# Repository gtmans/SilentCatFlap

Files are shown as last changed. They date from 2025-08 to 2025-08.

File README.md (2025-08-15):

# SilentCatFlap (Sure Flap MOD)
My cat used to get startled by the loud click the flap made whenever his microchip was detected.
To solve this, I replaced the original motor with a 28BYJ-48 stepper motor that moves smoothly and quietly.

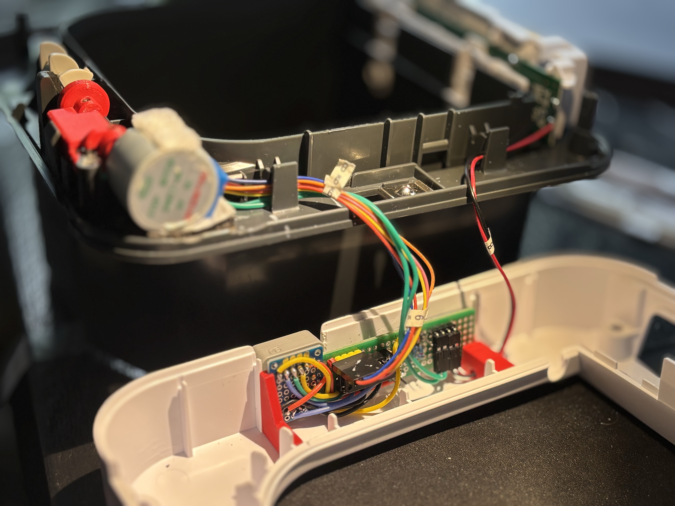
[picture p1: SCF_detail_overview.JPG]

The stock motor would drive loudly against a stop at -3 V to open and +3 V to close. In the first phase of the project, I kept as much of the existing cat flap electronics as possible, building a standalone controller that listens for those +3 V and -3 V signals and uses them to drive the stepper motor. The controller is powered by an M5 Atom Lite (about $10), which requires an external USB‑C power adapter. The stepper motor itself needs minor modifications — swapping the connector and removing a few protruding tabs.<BR><BR>

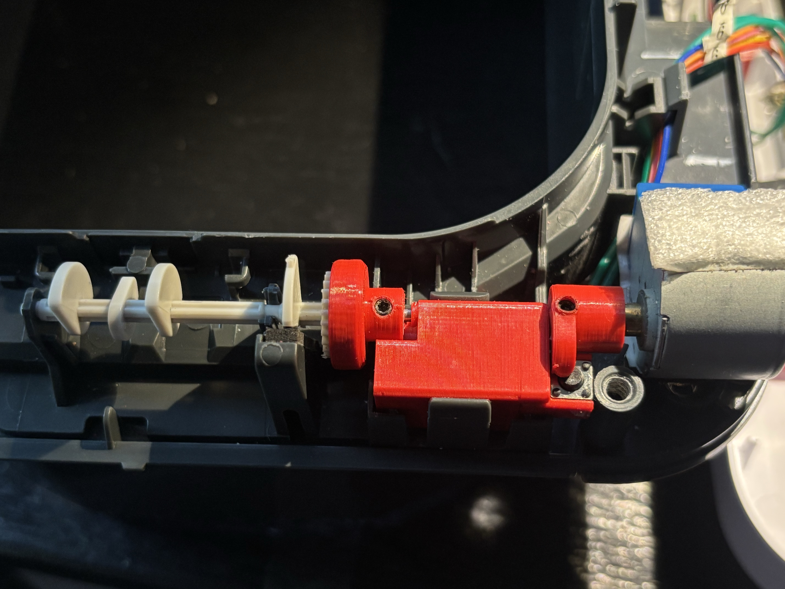
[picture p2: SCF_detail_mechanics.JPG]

From the accompanying ULN2003 driver board, I only use the driver IC, which I mounted onto a small custom PCB (see Fritzing layout). I also designed several custom parts for 3D printing (see .stl files). The build additionally uses a 2 mm shaft and two screws from a shaft collar, 3 10K resistors, 1 diode, some wire and a tiny microswitch.

Finally, a few small adjustments to the original cat flap housing are necessary to ensure that all moving parts operate freely.<BR>

tiny video: https://youtu.be/TwItX0s3qm8 <BR>Tinkercad model: https://www.tinkercad.com/things/aXRrV4Vo9WM-silentcatflap-parts-shared <BR><BR>
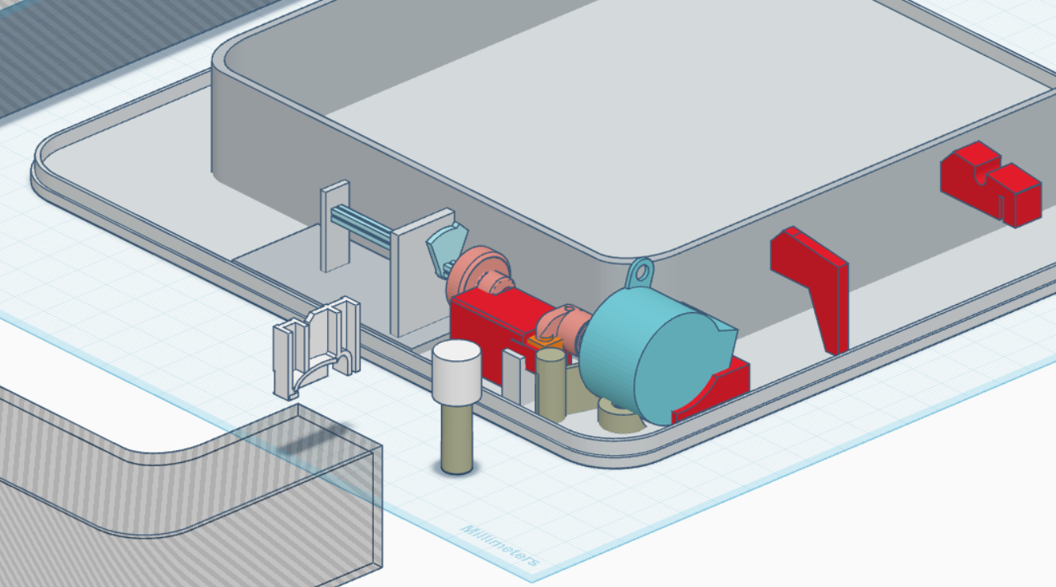
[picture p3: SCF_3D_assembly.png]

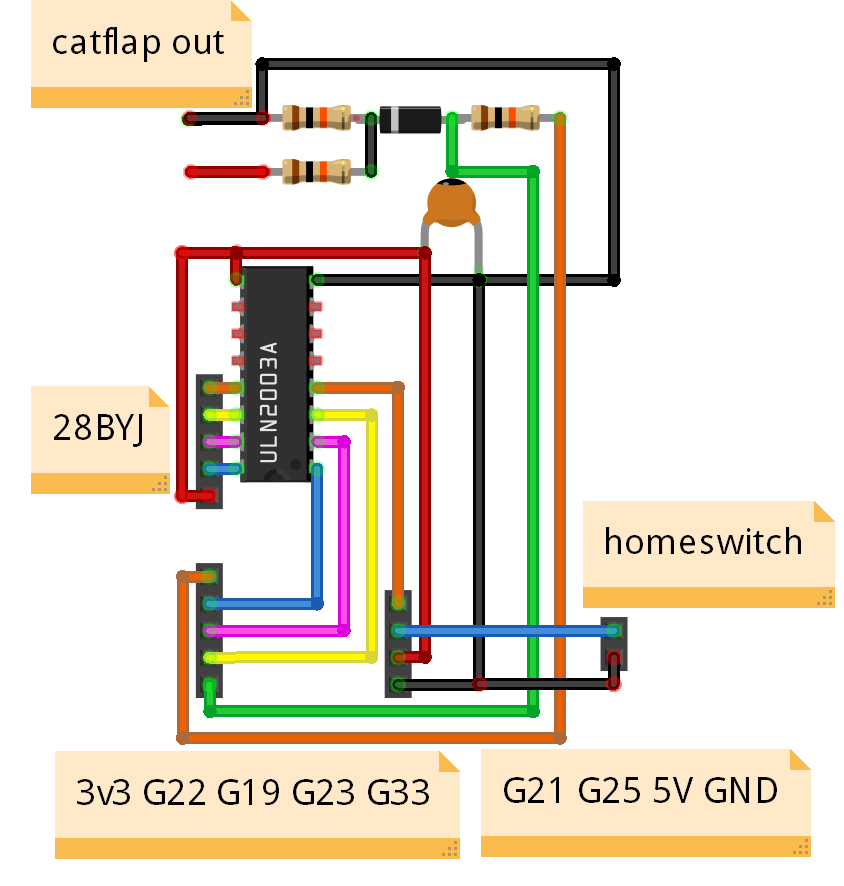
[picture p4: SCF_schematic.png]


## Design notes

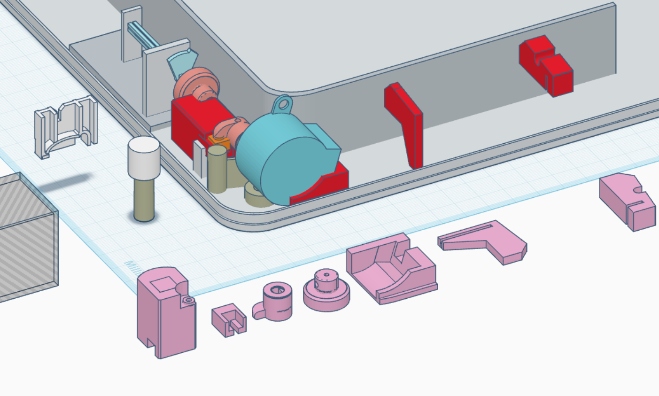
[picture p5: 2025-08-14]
SCF_3D_paerts_overview.png

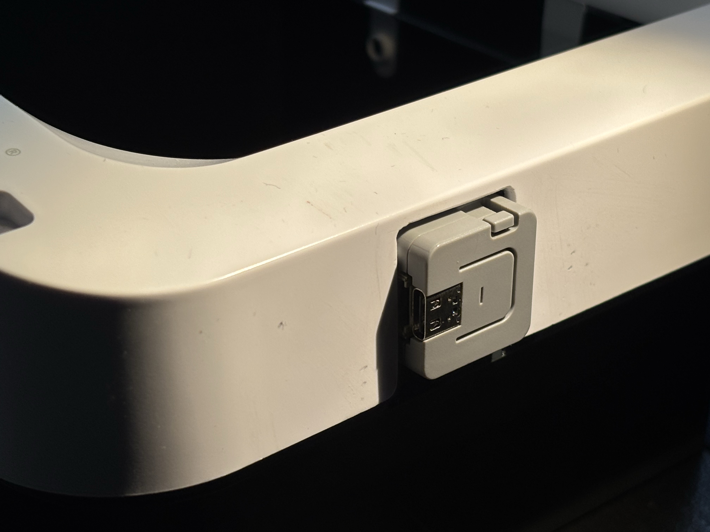
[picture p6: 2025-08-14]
SCF_detail_outside.JPG

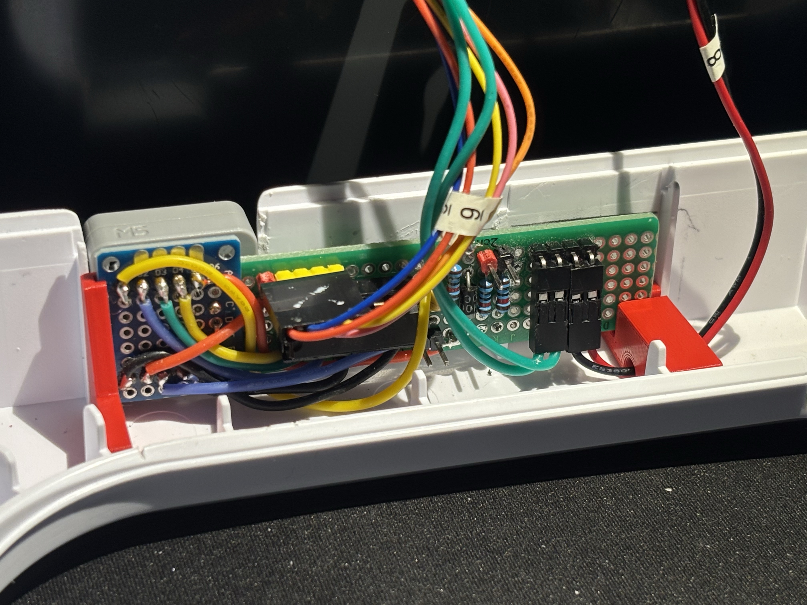
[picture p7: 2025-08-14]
SCF_detail_perfboard.JPG

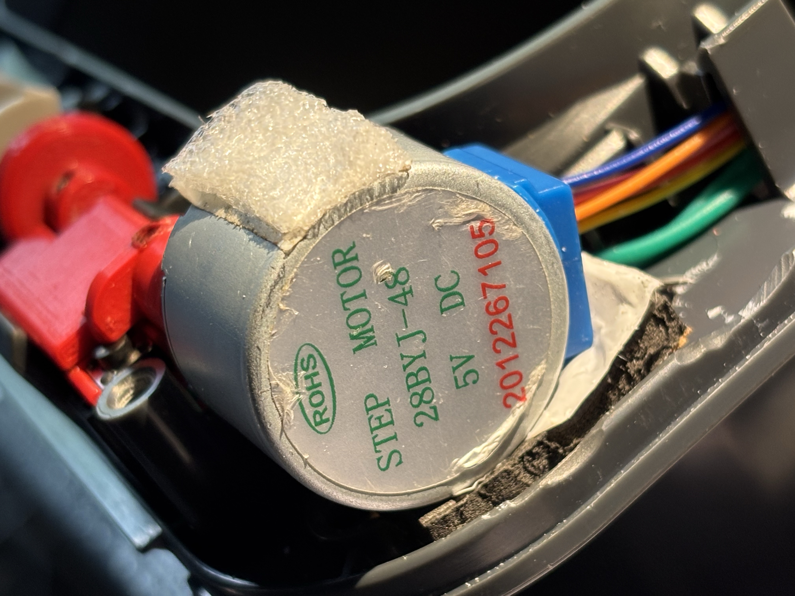
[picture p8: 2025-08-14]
SCF_detail_steppen.JPG

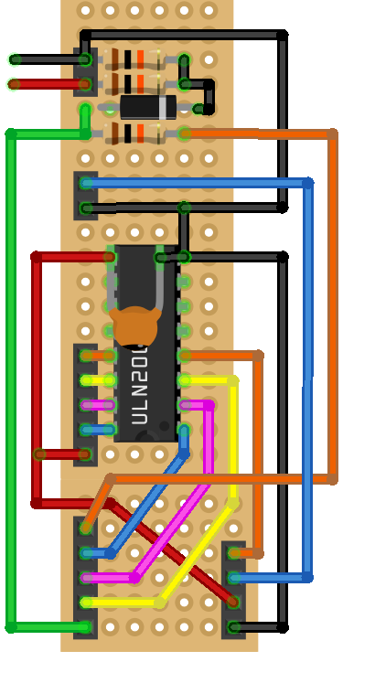
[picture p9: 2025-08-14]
SCF_perfboard.png

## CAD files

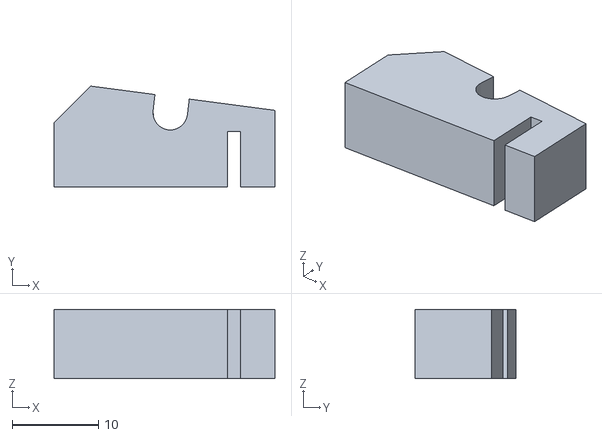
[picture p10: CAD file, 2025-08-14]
SilentCatFlap-print_holder1.stl
25.6 x 11.7 x 8.00

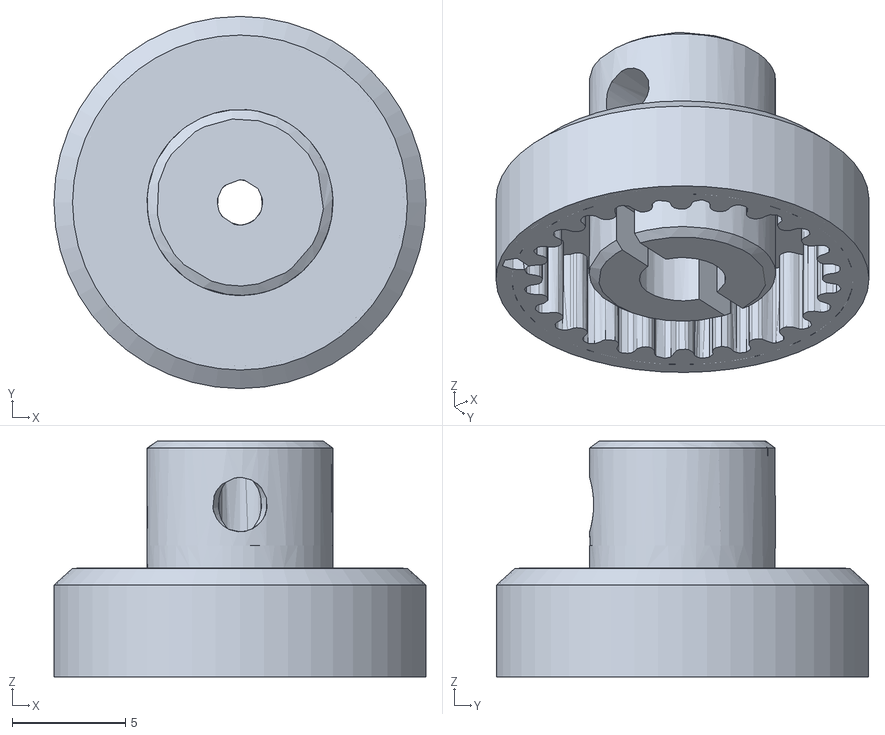
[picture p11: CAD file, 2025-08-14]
SilentCatFlap-gear_wheel.stl
16.4 x 16.4 x 10.4

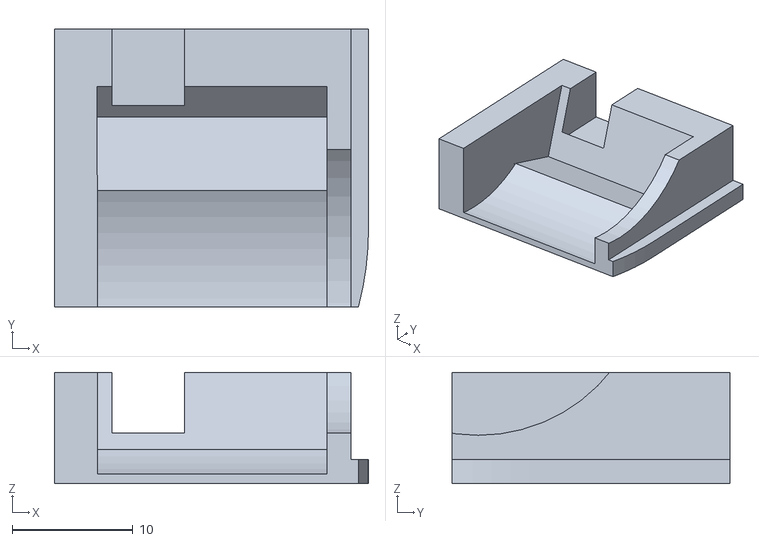
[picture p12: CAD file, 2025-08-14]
SilentCatFlap-steppen_holder(not used).stl
26.0 x 23.0 x 9.20

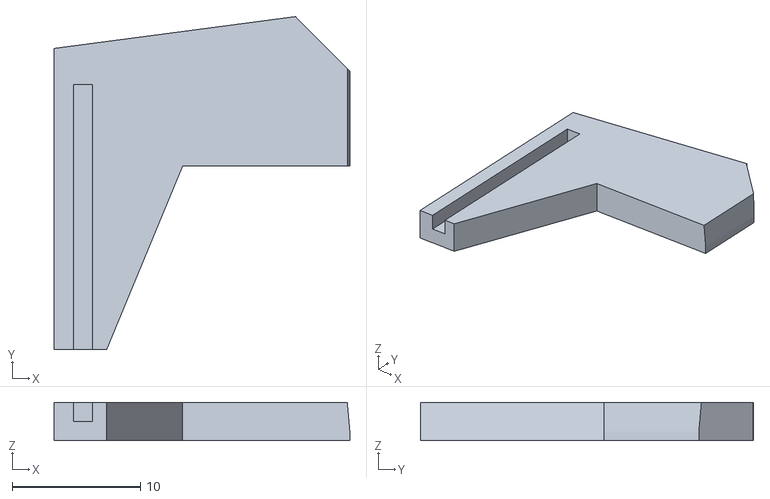
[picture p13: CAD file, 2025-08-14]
SilentCatFlap-print_holder2.stl
23.1 x 26.0 x 3.00

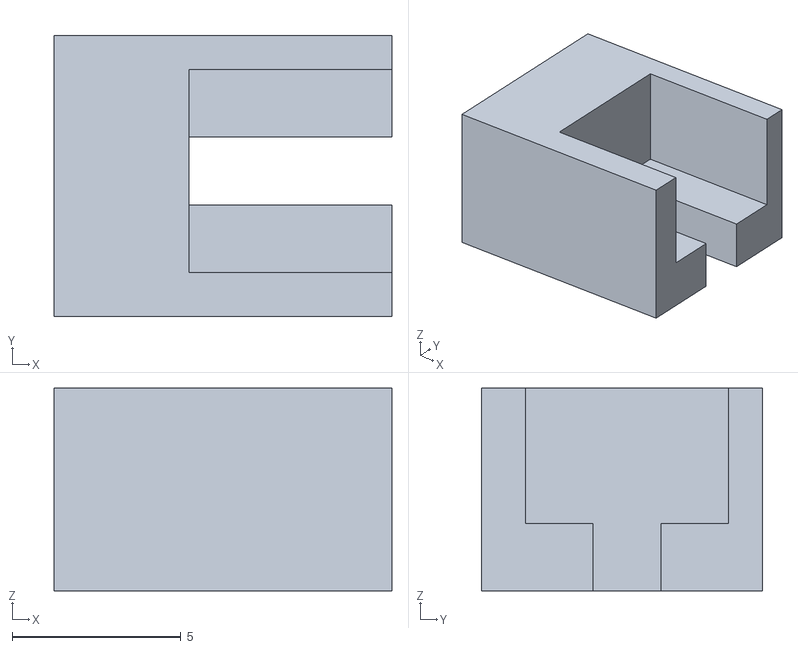
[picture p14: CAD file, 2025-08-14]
SilentCatFlap-switch_holder.stl
10.0 x 8.30 x 6.00

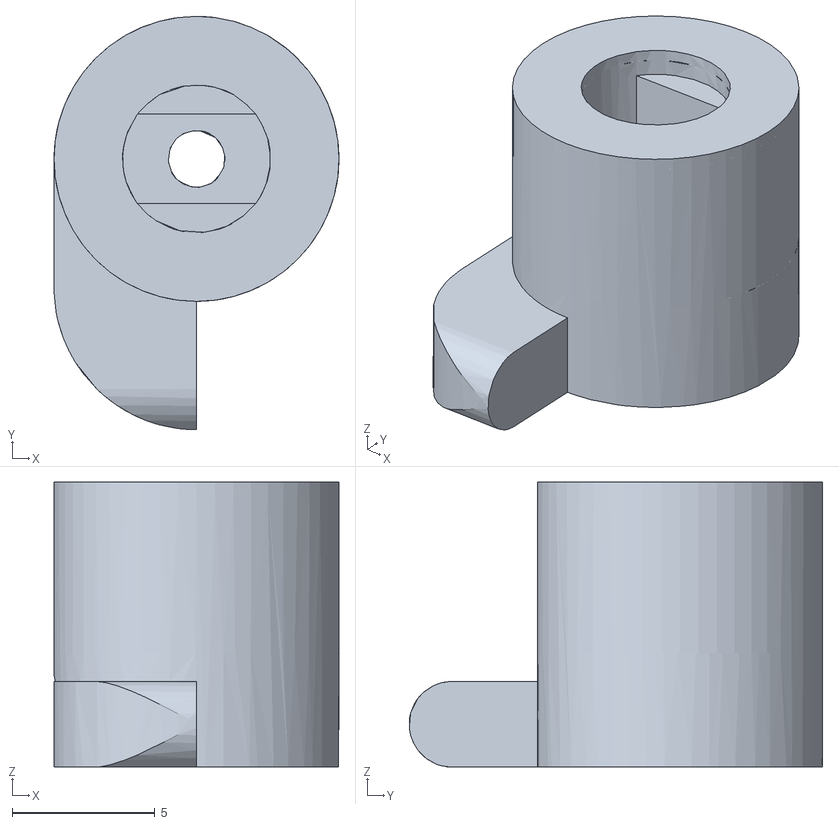
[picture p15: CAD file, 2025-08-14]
SilentCatFlap-steppen_wheel.stl
10.00 x 14.5 x 10.00

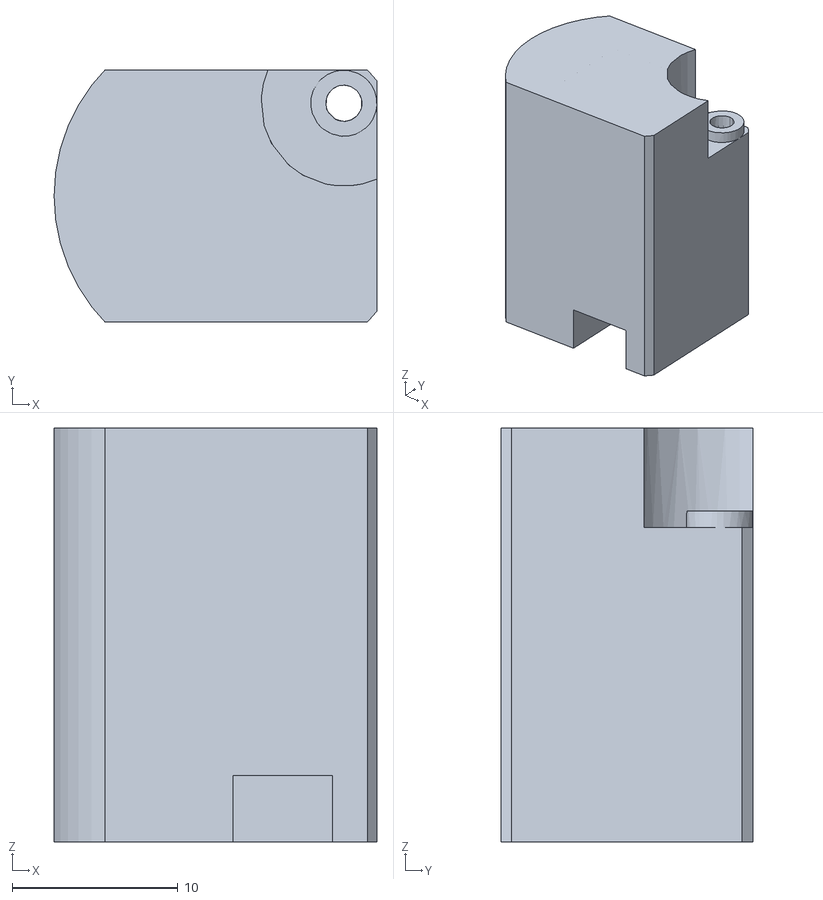
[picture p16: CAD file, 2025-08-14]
SilentCatFlap-dummy_motor.stl
19.5 x 15.2 x 25.0

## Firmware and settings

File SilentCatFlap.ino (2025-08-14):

// SilentCatFlap 2025 gtmans github
/*
parts:
- M5 Atom light
- 28BYJ-48 with ULN2003
- microswitch

hardware setup:
to read serial port 33 on atom to detect +3, -3 or 0v
GNDIN ----------+------------------ GND     catflap black to M5 GND
               10K
                +-- |<-DIODE --+--- GPIO33  (serial pin)
               10K            10K
UNKNWN*---------+              +--- 3v3     *catflap red to M5 +3.3v

pin connectors:
XX      [25] [GND]             ← microswitch
X IN1   [22]                   ← steppenmotor 28BYJ blue
X IN2   [19]                   ← steppenmotor 28BYJ pink
X IN3   [23]                   ← steppenmotor 28BYJ yellow
X IN4   [21]                   ← steppenmotor 28BYJ orange
*/

#include    "M5Atom.h"
const int   analogPin   = 33; 
bool        flapopen,lastflap,flapchg;
bool        triggered   = false;
int         sensorValue,flap,flapRaw,flapstat;
const int   samples     = 3;
int         dimcnt;

#define     STOPSWITCH_PIN  25
int homing_count;

#include    <Stepper.h>
#define     IN1 22
#define     IN2 19
#define     IN3 23
#define     IN4 21
const int   STEPS_PER_REV   = 2039;
const int   ANGLE_140_STEPS = 793;
const int   DEG10 = ANGLE_140_STEPS/14;
int         degcnt,degsteps,stp,stpmax=30;//18 steps

Stepper myStepper   (STEPS_PER_REV, IN1, IN3, IN2, IN4);

void setup() {
  M5.begin          (true, false, true);
  delay             (50);
  myStepper.setSpeed(12);// 10=OK, 14 Not working
  Serial.println    ();
  Serial.println    (__FILE__);
  pinMode           (STOPSWITCH_PIN, INPUT_PULLUP); // schakelaar naar GND
  pinMode           (IN1, OUTPUT);
  pinMode           (IN2, OUTPUT);
  pinMode           (IN3, OUTPUT);
  pinMode           (IN4, OUTPUT);
  homing            ();
//showoff after power on: remove if not wanted
  openflap          ();
  delay             (2000);
  closeflap         ();
//end of demo
}

void redlights(){
  for (int i=0;i<6;i++){
    M5.dis.drawpix    (0, 0xff0000);//red
    delay (500);
    M5.dis.drawpix    (0, 0x000000);
    delay (500);
  }
}
void openflap(){
  Serial.println  ("openflap()");
  while           (digitalRead(STOPSWITCH_PIN)!=LOW){redlights();homing();}// not fully open safe escape
  Serial.println  (String(stpmax*DEG10)+" stappen vooruit!");
  myStepper.step  (-stpmax*DEG10);
  releaseMotor    ();
  flapstat    =   2;
  flapopen    =   true;
  M5.dis.drawpix  (0, 0x00ff00);//green
  dimcnt      =   0;
}

void closeflap(){
  Serial.println  ("closeflap()");
  stp         =   stpmax;
  int stapjes =   0;
  while (digitalRead(STOPSWITCH_PIN)!=LOW){
  //Serial.print  (stp);
  //Serial.print  ("-");
    stp--;
    if (stp<0)    {break;}
    myStepper.step(DEG10);
    stapjes +=    DEG10;
  }  
  Serial.println  (" "+String(stapjes)+" stappen terug!");
  releaseMotor    ();
  flapstat    =   1;
  flapopen    =   false;
  M5.dis.drawpix  (0, 0xff0000);//red
  dimcnt      =   0;
}

void homing(){            // naar referentiepunt
  M5.dis.drawpix    (0, 0x0000ff);//blue
  Serial.print            ("homing()");
  homing_count     =      0;
  while(digitalRead       (STOPSWITCH_PIN) == HIGH && homing_count < stpmax*2) {
    myStepper.step        (DEG10/2);
    homing_count++;
    delay(2);
  }
  releaseMotor    ();
  Serial.println          (digitalRead(STOPSWITCH_PIN)==LOW ? "gevonden!" : "niet gevonden!");
  Serial.println          ("homing_count:"+String(homing_count/2));
  if (digitalRead         (STOPSWITCH_PIN)==LOW){flapopen=false;}else{flapopen=true;}
}

void loop() {
  M5.update();            // Read the press state of the key.
  if (M5.Btn.wasPressed()) {
    Serial.print          (flapstat);
    if (digitalRead       (STOPSWITCH_PIN)==LOW){//closed
      flapstat    =       2;
    } else  {
      flapstat    =       1;
    }  
    flapchg       =       true;
    Serial.println        (flapstat);
  } else {readFlap();}
  if (flapchg){
    Serial.println        ("flapopen:"+String(flapopen)+" flapstat:"+String(flapstat));  
    switch (flapstat){
    case 0:  // none
      //M5.dis.drawpix    (0, 0x0000ff);//blue
        Serial.print      ("0V");
        break;
    case 1:  // do close
      //M5.dis.drawpix    (0, 0xff0000);//red
        Serial.println    ("CLOSE -3v send CLOSE CMD");
        closeflap         ();
        break;
    case 2:  // do open
      //M5.dis.drawpix    (0, 0x00ff00);//green
        Serial.println    ("OPEN +3v send OPEN CMD");
        openflap          ();
        break;
    }
    Serial.println        ("flapopen:"+String(flapopen)+" flapstat:"+String(flapstat)); 
  }
  if (triggered){
    M5.dis.drawpix        (0, 0x800080);//pink
    Serial.print          ("Waiting ...");
    delay                 (15000);
    Serial.println        ("Auto close flap after 15 seconds");
    triggered   =         false;
    closeflap             ();
    M5.dis.drawpix        (0, 0xff0000);//close
  } else                  {delay(100);}
  dimcnt++;
  if (dimcnt>600)         {dimcnt=0;M5.dis.drawpix(0, 0x000000);}//prox 1 minute
}

void releaseMotor() {
  digitalWrite            (IN1, LOW);
  digitalWrite            (IN2, LOW);
  digitalWrite            (IN3, LOW);
  digitalWrite            (IN4, LOW);
}

void readFlap() {
  lastflap    =           flapopen;
  flapRaw     =           0;
  for (int i  = 0; i < samples; i++) {
    flapRaw  += analogRead(analogPin);
    delay                 (3);
  }  
  flap        =           flapRaw/samples;
  if         (flap<500)   {//-3V
    flapopen  =           true; //do open
    flapstat  =           2;    //open
    triggered =           true;
  } else if  (flap>2200) {//3V
    flapopen  =           false;//do close
    flapstat  =           1;    //close
  } else {
    flapstat  =           0;    //none
  }
  if (lastflap!=flapopen) {flapchg=true;}else{flapchg=false;}
}
